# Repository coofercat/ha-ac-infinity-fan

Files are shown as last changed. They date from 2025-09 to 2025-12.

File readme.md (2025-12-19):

# HA AC Infinity Fan Controller

The AC Infinity Cloudline growing fans (such as the S4, S5, S6) are fantastic smart fans. They're made for growing rooms and the like, but also have a use in domestic bathrooms. They have temperature and humidistat probes and can be programmed to speed up the fan as humidity increases. This makes them ideal to suck out the steam after a shower.

Side note: in the UK, all houses have to have an Energy Performance Certificate (EPC). EPCs now take into account things like ventilation, energy efficiency etc. Smart fans can help improve your EPC because you can show continuous forced ventilation, and variable speed extraction of humidity (which is better than running on
a timer, or even at full speed to a fixed humidity level).

Whilst AC Infinity fans can connect to Wifi or Bluetooth, sadly, they do not (yet) come with any publicly accessible API. As such, the likes of Home Assistant can't directly interface with them. Hopefully one day AC Infinity will see the value in such things, but until then, we have to use different methods to hook these fans into our home automation.

## About This Project

__Note: The suggested PCB suffers from electrical noise problems. It worked fine on the desk, but in actual use, it's not really good enough. I'm working on a solution...__

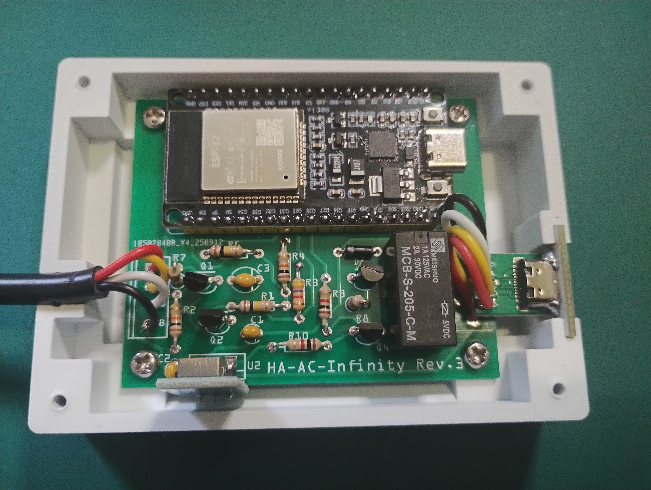
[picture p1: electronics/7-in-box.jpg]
[](electronics/7-in-box.jpg)

This project aims to provide Home Assistant integration to AC Infinity Cloudline fans, but also aims to leave all the original manufacturer functionality in place. This allows for flexibility and creativity in Home Assistant, but leaves the fans "as intended" and usable by any future owners.

In terms of implementation, this project puts some electronics "between" the AC Infinity controller display and the fan itself. It's entirely powered by the fan, and unless Home Assistant instructs it otherwise, it just passes AC Infinity signals from the controller to the fan completely unaltered.

Home Assistant is able to read the speed requested by the AC Infinity controller, the actual speed of the fan itself (via its tach signal), and is able to "switch out" the controller and provide signals to drive the fan itself if needed. There is no way to read the temperature or humidistat sensors on the AC Infinity controller though (if that's required, other projects may be more to your liking than this one).

Since this project was for use in bathrooms, we also provides an optional Boost Button. That is, a button which can be used to request 30 minutes of maximum speed fan extraction, perhaps to remove smells. The button is completely optional and does not require Home Assistant to be running or available to make it work.

The whole thing is based around an ESP32-32S WROOM (CP2012) and ESPHome. A few pins of the ESP are used as inputs and outputs, the bluetooth is used as a BLE receiver (for the Boost Button), the Wifi connects it to Home Assistant.

## Documentation

- [About the Electronics](electronics/readme.md)
  - [Electronics 3D Printed box](electronics/3d-printer/readme.md)
- [About the Boost Button](boost-button/readme.md)
  - [Boost Button 3d Printed box](boot-button/3d-printer/readme.md)
- [About the ESPHomeSoftware](esphome/readme.md)
- [FAQ](faq.md)
- [License](LICENSE.md)

## Authors Note

This project is Creative Commons licensed, so you're pretty much free to do what you like with it, so long as you credit the original author. If you do make it, we'd love to hear about what you're doing with it though, so please do get in contact.

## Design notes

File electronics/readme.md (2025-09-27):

# HA AC Infinity Electronics

The electronics for the HA AC Infinity project require a few components:

- An ESP32-32S WROOM board (eg. https://www.amazon.co.uk/dp/B0DQ51N5B1)
- A USB-C socket (eg. https://www.amazon.co.uk/dp/B0D59Y34ZF)
- A USB-C plug (eg. https://www.amazon.co.uk/dp/B09V273Z8Z)
- Some 4-core wire (eg. https://www.amazon.co.uk/dp/B0C14L4W14)
- Two 3D printed parts to make the box (although other boxes are also possible)
- Four M3 x 5mm and 4 M3 x 12mm screws to hold it together
- Some short lengths of general purpose multi-strand hookup wire (ideally in a few different colours)

There is also a whole [Bill Of Materials](https://html-preview.github.io/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) (BOM) for the electronic circuit. The circuit uses mostly generic, easy to source through-hole components. It's relatively easy to solder together. The transistors I used are 2N3904, and I used a buck module (https://www.amazon.co.uk/dp/B081JMJZG6) instead of a regular 7805 voltage regulator (if you do use a 7805, you will also need a heatsink). The relay is a generic 5V coil, DPDT (I had some of these already). The BOM lists JP1 and JP2, but these are not needed - they're just holes for attaching wires.

I also had PCBs made, which is optional but recommended (you get a lot of electrical noise in this circuit, so trying to make it work on a breadboard or stripboard is likely to be difficult). There is a [Fritzing file](ac-infinity-esphome.fzz) and [exported Gerber files](ha-ac-infinity-gerber-export/) available if you want to make a PCB.

## Making the Electronics

### USB Connectors

AC Infinity misuse USB connectors for their proprietary connections. Their system is absolutely not compatible with any genuine USB devices, and will likely catastrophically damage them if you are foolish enough to connect them to it.

For the project, we need a lead with a plug on the end of it and a socket. The plug likely can't fit any plastic covers on it, and the lead should be long enough to allow you to put the box of electronics somewhere near to the fan's controller. In my case they're all hidden away, so I've used a short cable. Longer cables are likely possible because the signals used aren't particularly complex.

| Socket & Plug | AC Infinity | Colour Coding |
| --- | --- | --- |
| V | +10V | Red |
| D+ | Tach Signal | Yellow |
| D- | PWM | White |
| G | Ground | Black |

Note the labelling on the plug and socket is really small - be careful where you're soldering!

For the plug, cut about 30cm of the four core cable. Remove about 15mm of sleeve from one end to expose the individual wires. Then strip all four wires to a couple of millimeters (I found it easier to strip to about 5mm and trim them after tinning). Tin the ends, and tin all four pads on the plug. Then you can connect the wires to the pads relatively easily. At the other end of the cable, remove maybe 15-20mm of sleeve and then strip the wires to about 5mm (don't tin them though).

For the socket, you need four 50mm lengths of multi-strand wire. Strip one end to a couple of millimeters, insert into the holes on the socket and solder into place. Again, strip the other end to maybe 5mm, but don't tin them.

| USB Plug Wiring | USB Socket Wiring |
| --- | --- |
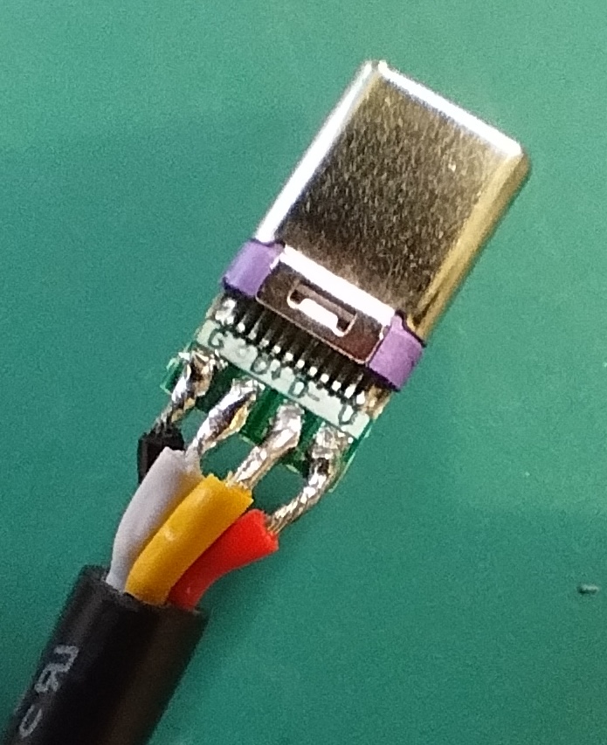
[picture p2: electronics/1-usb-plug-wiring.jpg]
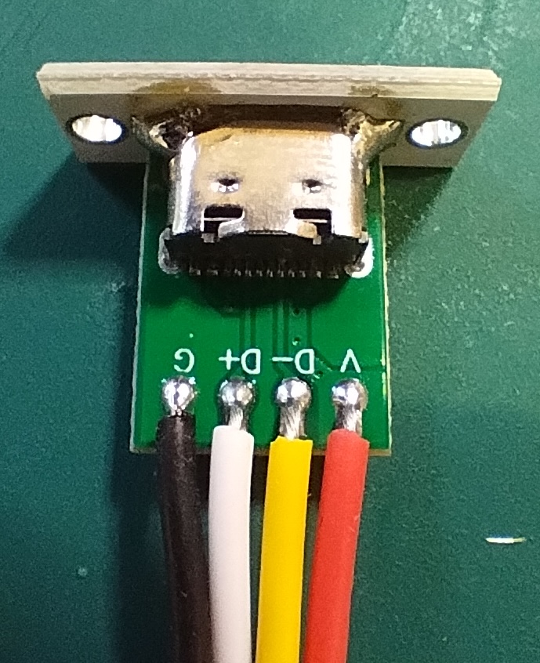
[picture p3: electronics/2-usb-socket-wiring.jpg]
| [](1-usb-plug-wiring.jpg) | [](2-usb-socket-wiring.jpg) |

### Making the PCB

The PCB uses through-hole components, which are hopefully easy to fit and solder. Most components lie against the board, although a few resistors are vertical (R7 & R8). Please note that if a 7805 voltage regulator is used (instead of a compatible module) then a heat sink will be required.

See the [Bill Of Materials](https://html-preview.github.io/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) for a full list of components required and where to fit them. Note that JP1 and JP2 are not required - instead their holes can be used to connect wires from the USB sockets (see below).

| Step | Step |
| --- | --- |
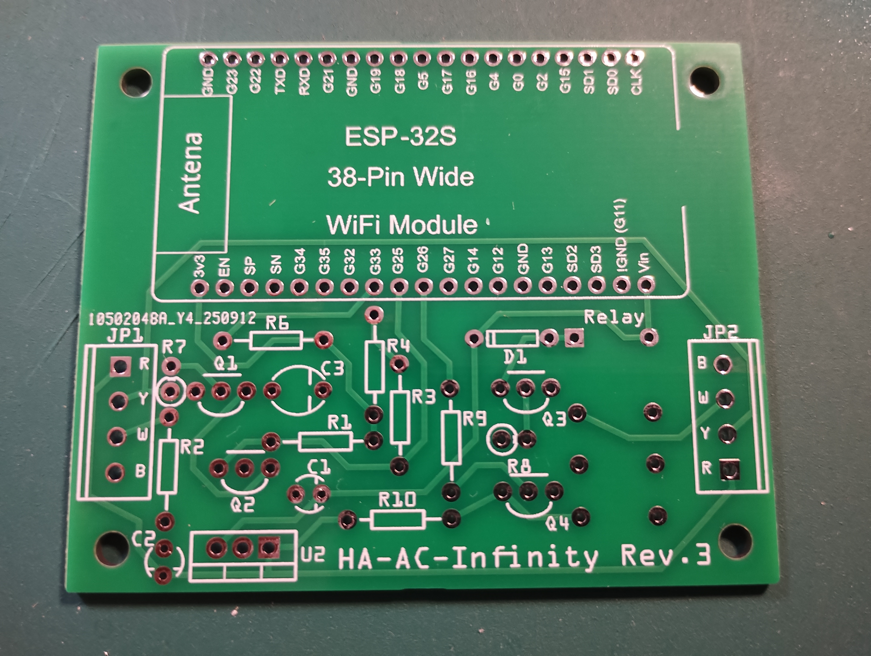
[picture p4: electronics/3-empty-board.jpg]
| [](3-empty-board.jpg) | Start with an empty board...  |
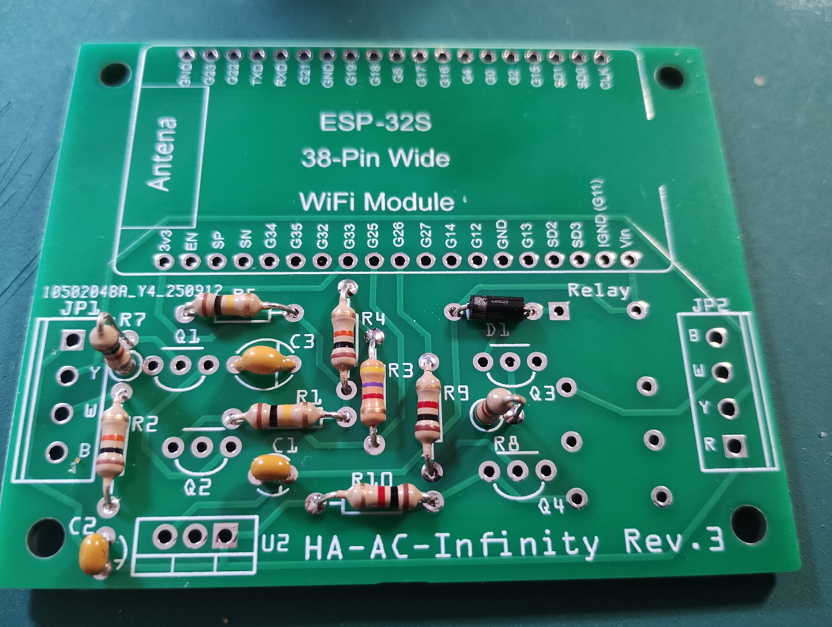
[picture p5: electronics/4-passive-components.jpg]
| [](4-passive-components.jpg) | Add the passive components... |
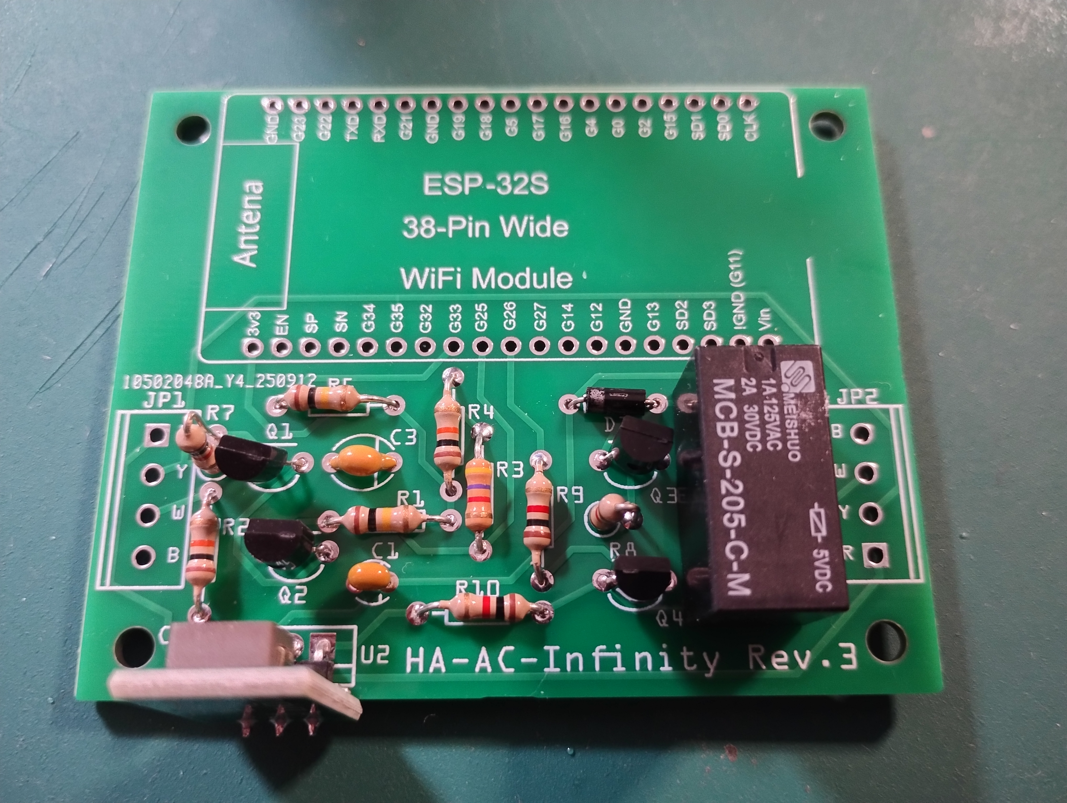
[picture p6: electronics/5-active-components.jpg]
| [](5-active-components.jpg) | Add the active components...  |

### Connecting the USB Connectors

The left hand JP1 connector is used to connect the USB plug, on the 4 core cable. The right hand, JP2 connector is used to connect the USB socket, on four short multi-strand wires. Note the colour coding of the holes on the PCB, from the top of the board to the bottom:

| JP1 | JP2 |
| --- | --- |
| Red | Black  |
| Yellow | White  |
| White  | Yellow |
| Black  | Red |

Once assesmbled it should look like this:

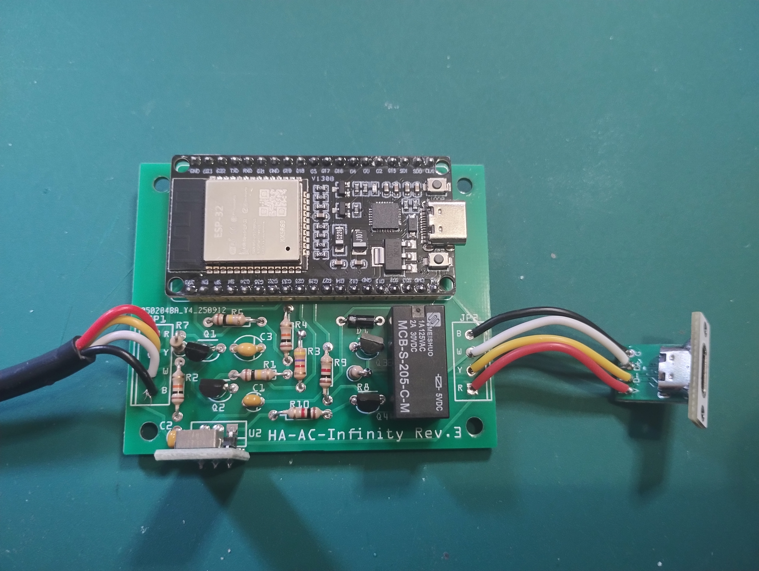
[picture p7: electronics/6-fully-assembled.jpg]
[](6-fully-assembled.jpg)

### Fitting the board into the box

The board should screw into the box using four M3 5mm self-tapping screws. The 4 core cable should fit into the cable gland, and be held into place by a strain-relief grip. The USB socket should fit into the slot on the side of the box.

[](7-in-box.jpg)

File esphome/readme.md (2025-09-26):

# ESPHome Software

This software requires [ESPHome](https://esphome.io/) to be on the ESP32 before it can be used.

Once ESPHome is installed, the [device.yaml](device.yaml) file can be pasted into the device configuration. Some secrets need to be added to ESPHome, or else edit the yaml appropriately.

The code has a configurable section:

```
  name: "ac-infinity-fan-1"
  friendly_name: "ac-infinity-fan-1"
  ap_ssid: "ha-ac-infinity-fan-1"
  ap_password: "ha-ac-infinity"
  ha_api_encryption_key: !secret ha_api_encryption
  esphome_ota_password: !secret esphome_ota_password
  wifi_connect_ssid: !secret wifi_ssid
  wifi_connect_password: !secret wifi_password
  boost_minutes: "30"
  boost_button_mac_address: "00:11:22:33:44:55"
  calibration_mode: "false"
```

| Variable | Comments |
| --- | --- |
| name | The ESPHome/HA name for the device |
| friendly_name | The longer name used to describe the device in the UI |
| ap_ssid | The network name (SSID) to create if wifi cannot be found during boot up |
| ap_password | The network password of the mini access point created if wifi not found during boot up |
| ha_api_encryption_key | The Home Assistant API encryption key _where to get this?_ |
| esphome_ota_password | The password used by ESPHome when making Over The Air (OTA) wireless connections |
| wifi_connect_ssid | The network name (SSID) of the wifi network to connect to on boot up |
| wifi_connect_password | The network password of the wifi used to connect to on boot up |
| boost_minutes | The number of minutes to run the fan during Boost Mode (specify as a string with quotes around the number) |
| boost_button_mac_address | A MAC address to listen for, if found, activate Boost Mode |
| calibration_mode | Boolean to enable calibration mode (see below) |

## Calibration

The project uses whole numbers from 0-10 to denote the speed of the fan (in the same way as AC Infinity do in their app and on the controller). To make these match with the AC Infinity scale, we have to calibrate the software to match.

Calibration Mode shows a decimal part of the integer speed number. This is a fraction of the "distance" between the lower and upper thresholds of a given speed number. For example, if the lower threshold was 1000 and the upper was 2000, and the current reading was 1230, then the decimal would be .23.

Working out thresholds requires some experimentation and measurements of the actual values received from the fan and controller. Hopefully the values provided here work in most cases, buf if you find selecting (say) speed 3 in the controller shows speed 4 in the Home Assistant UI, then some calibration may be required.

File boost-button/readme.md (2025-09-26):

# HA-AC-Infinity Boost Button

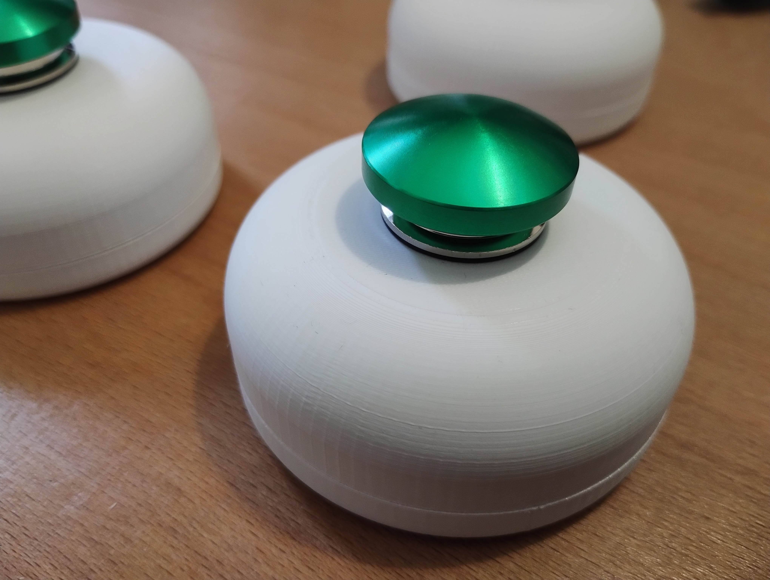
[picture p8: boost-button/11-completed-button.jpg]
[](11-completed-button.jpg)

The Boost Button is a way to request the fan comes on (at full speed)
for a period of time (currently programmed at 30 minutes). It's a
physical device with a big button on the top which can be put somewhere
in the bathroom, should anyone, er, "make smells" and want to have
some ventilation.

Internally, the button is made of some bought components:

- A so-called "iTag" key finder (BLE beacon), such as these: https://www.amazon.co.uk/dp/B0FH64TKKL
- A 22mm mushroom button, such as these: https://www.amazon.co.uk/dp/B0DB28T1KS
- Two AAA single battery holders, such as these: https://www.amazon.co.uk/dp/B0B9NJ14WL
- Some 3D printed parts to make a sort of "hockey puck" box
- Some small screws to hold things together (eg. 4 off M2.3 x 5-8mm round head, 2 off M2.3 x 5mm countersunk)

There are full [instructions](instructions.md) for how to construct the button.

## About the BLE Beacon

The "ITag" devices are super-cheap (you get four in pack for less than one of the "better" brands).
They're probably not very good at being key finders (mainly because the phone app they use is pretty poor),
but they work really well for this project.

These devices identify as "iTag", manufactured by "Ubiquitous Computing Technology Corporation". My scanner says they use the "Legacy" scanning type, and are LE only. They're connectable, and there are some capabilities once connected. The original phone app is able to make them beep remotely, so there's presumably a capability to do that in there somewhere.

The main feature that they need is that they must BLE beacon as soon as they're powered up. Some
brands do this, some do not (those tend to need you to press the button to start the beaconing
process). The Boostt Button has a single button, which we use to isolate power from the beacon to
specifically stop it beaconing (and to save battery). As such, we really do need it to start
beaconing as soon as we power it up. Some other brands of key finder can have their buttons
permanently pressed to do the same thing - if you can't find the iTag type, then some
experimentation may be needed.

You may want to look into using a phone app BLE scanner. I've been using nRF Connect (by Nordic Semiconductor). It seems to do a good job of finding these sorts of tags and giving out as much information as they have in them.

## About the Box

The box for this is 3D printed. You can of course use a different box, and if you use different
beacons, you're going to have to modify the box at the very least, if not design it differently.
The same is true if you use a different type of button.

In terms of printing, the box needs support to be able to print it. On my BambuLabs A1, with a single
filament, the support was sufficiently easy to remove and left good enough quality inside (all the
outside surfaces print beautifully). If you've got multiple materials and can do fancy support then
you're likely to get better internal quality than I did, but I'm not sure it's all that necessary.

The box is made of two parts which screw together from the bottom. You need to undo four small screws to be able to change the batteries.

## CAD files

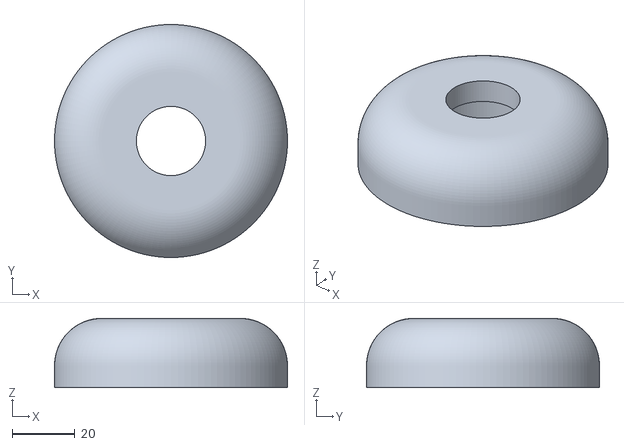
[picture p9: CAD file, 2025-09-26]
boost-button/3d-printer/button-top.stl
74.0 x 74.0 x 22.0

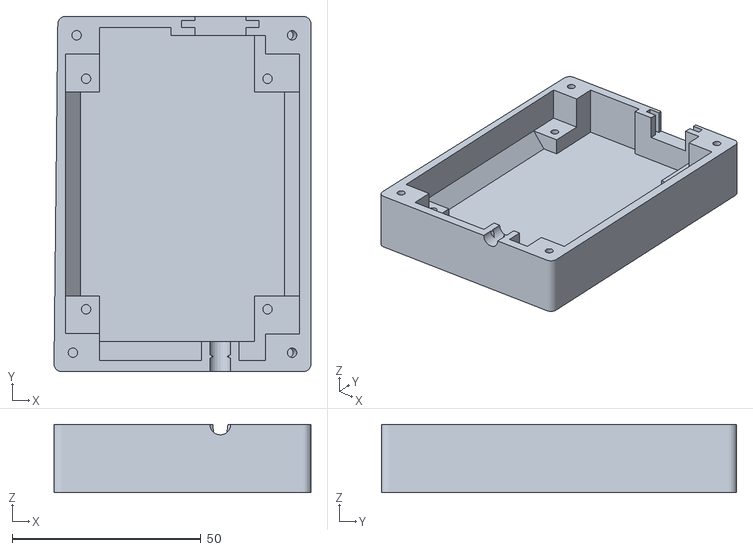
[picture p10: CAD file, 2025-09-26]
electronics/3d-printer/electronics-box-bottom.stl
68.0 x 94.0 x 18.0

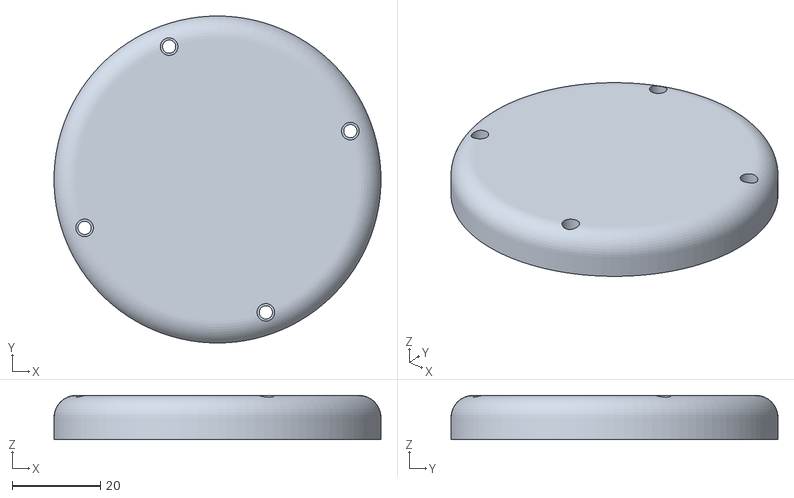
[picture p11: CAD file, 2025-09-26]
boost-button/3d-printer/button-bottom.stl
74.0 x 74.0 x 10.0

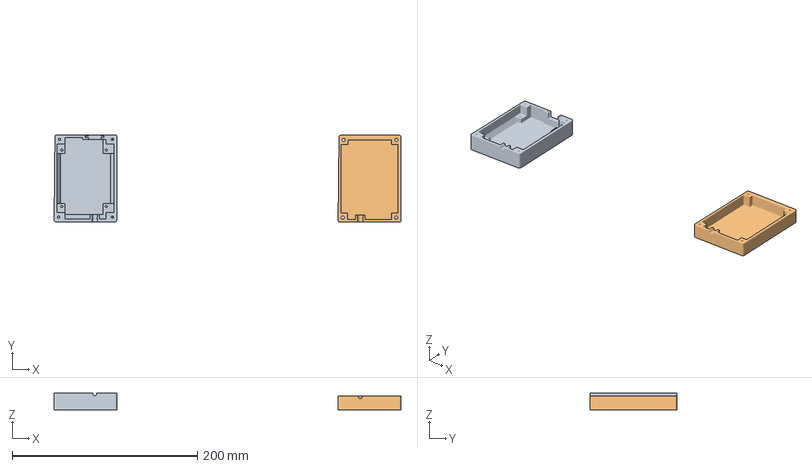
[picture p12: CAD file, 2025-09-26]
electronics/3d-printer/electronics-box.3mf
374.8 x 94.5 x 18.0 mm
electronics-box-bottom.stl
electronics-box-top.stl

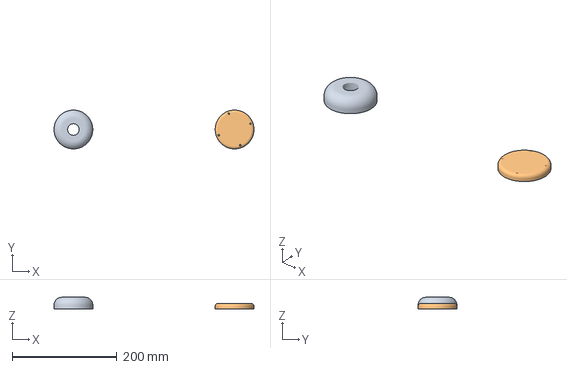
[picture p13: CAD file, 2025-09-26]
boost-button/3d-printer/boost-button.3mf
381.2 x 74.0 x 22.0 mm
button-top.stl
button-bottom.stl

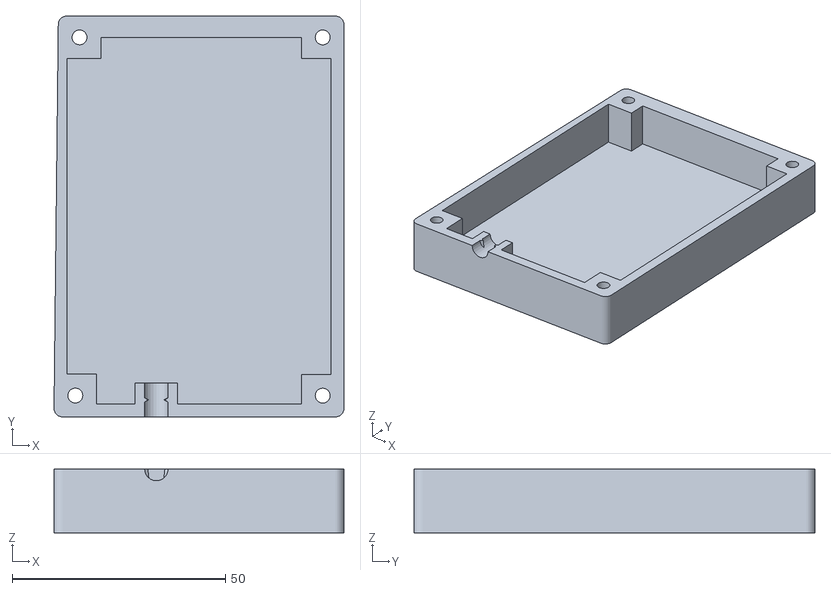
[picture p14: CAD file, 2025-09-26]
electronics/3d-printer/electronics-box-top.stl
68.0 x 94.0 x 15.0

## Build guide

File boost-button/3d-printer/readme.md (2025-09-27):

# Boost Button 3D Printed box

Three files are provided:

| File | Comments |
| --- | --- |
| [button-bottom.stl](button-bottom.stl) | The bottom lid of the button box, in STL format |
| [button-top.stl] (button-top.stl) | The top rounded part of the box, in STL format |
| [boost-button.3mf](boost-button.3mf) | Both top and bottom of the box in a Bambu Studio project file |

Both the top and bottom part need support to print successfully. On my Bambu AI with a single filament, support in "Normal Tree mode" worked well. Otherwise no special settings are required. Some experimentation may be required.

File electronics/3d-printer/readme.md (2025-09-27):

# Electronics 3D Printed Box

Three files are provided:

| File | Comments |
| --- | --- |
| [electronics-box-bottom.stl](electronics-box-bottom.stl) | The bottom of the box, in STL format |
| [electronics-box-top.stl](electronics-box-top.stl) | The top lid of the box, in STL format |
| [electronics-box.3mf](electronics-box.3mf) | Both top and bottom of the box in a Bambu Studio project file |

The electronics box is pretty easy to print in PLA filament (any colour). No special settings were required to print it successfully several times.

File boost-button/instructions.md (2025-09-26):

# Making the Boost Button

| Instructions | Picture |
| --- | --- |
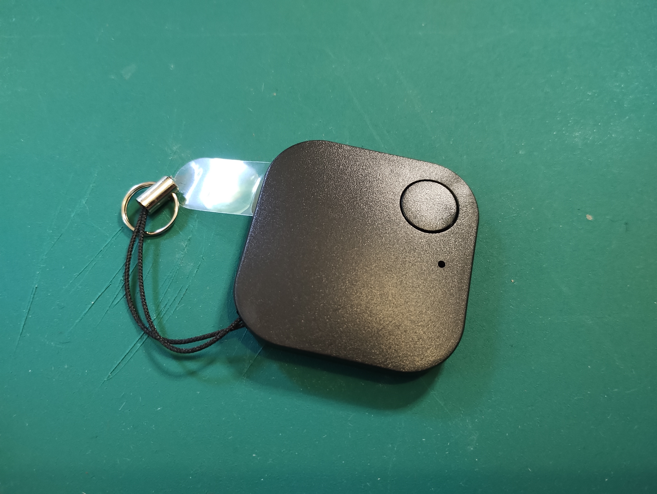
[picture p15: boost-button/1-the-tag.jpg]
| Firstly, take one of the keyfind fobs... | [](11-the-tag.jpg) |
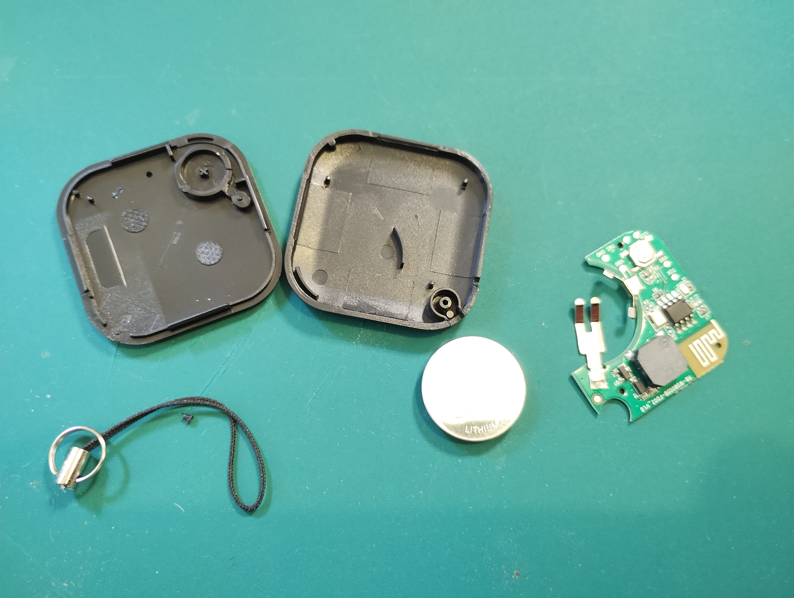
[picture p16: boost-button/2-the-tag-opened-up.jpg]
| ...and open it up. You can prize the two parts of the case apart, perhaps by inserting a small screwdriver in between them around the lanyard loop.| [](2-the-tag-opened-up.jpg) |
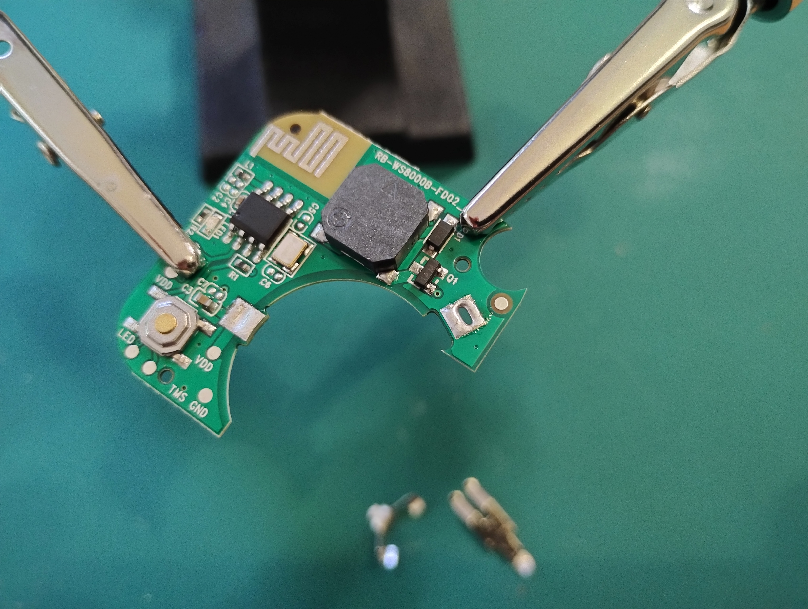
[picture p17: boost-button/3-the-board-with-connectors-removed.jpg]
| Take the circuit board and desolder the battery connectors. | [](3-the-board-with-connectors-removed.jpg) |
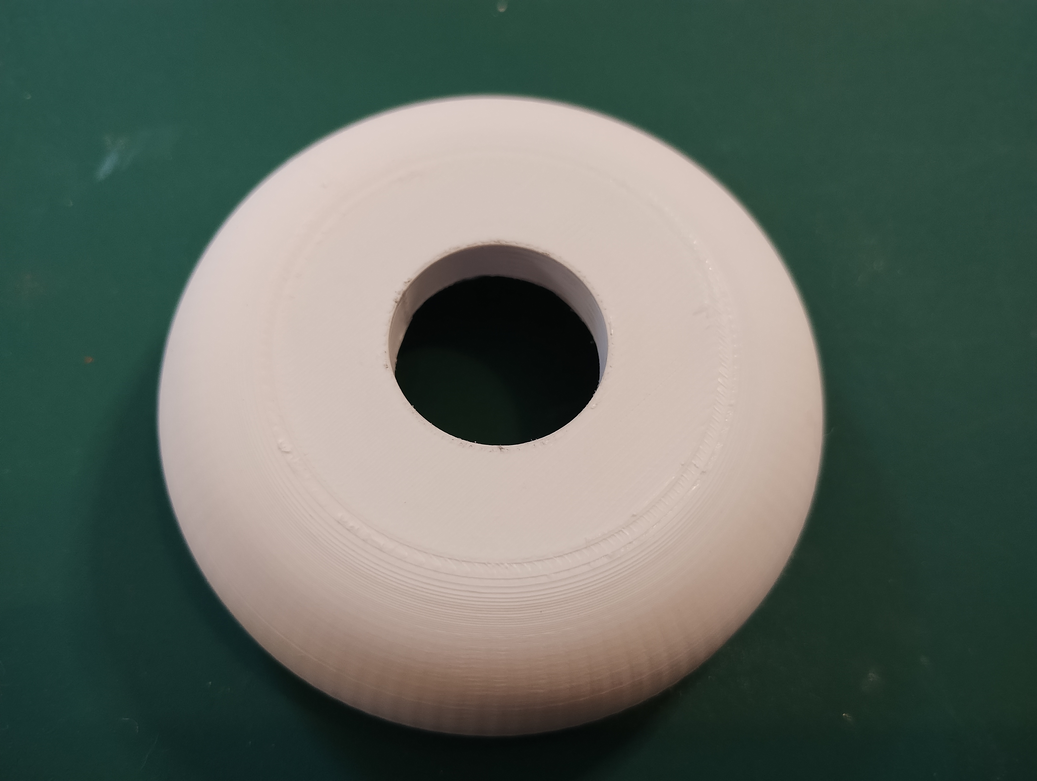
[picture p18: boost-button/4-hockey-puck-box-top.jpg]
| Take the top part of the hockey puck box... | [](4-hockey-puck-box-top.jpg) |
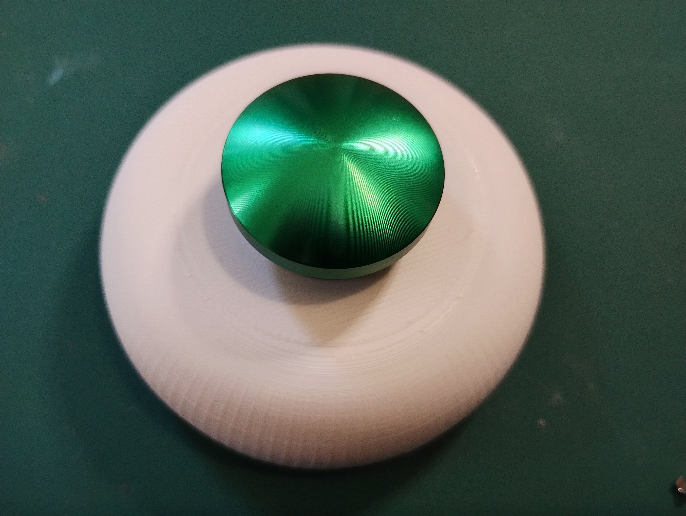
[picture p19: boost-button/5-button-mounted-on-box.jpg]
| Fit the mushroom button into the box. | [](5-button-mounted-on-box.jpg) |
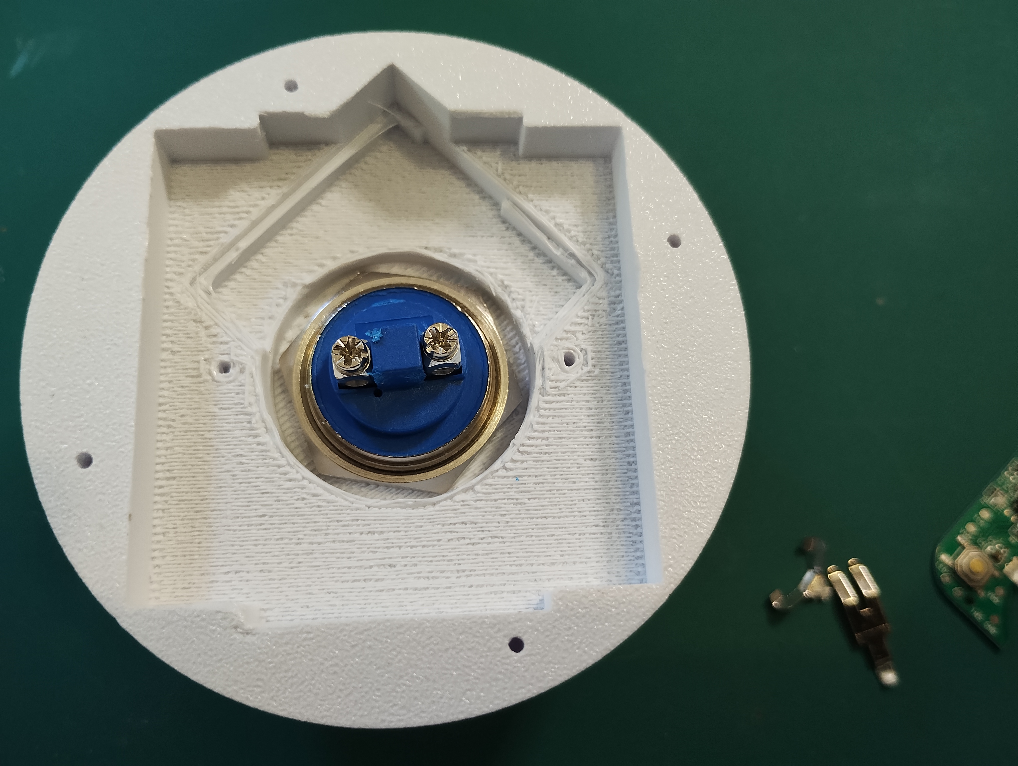
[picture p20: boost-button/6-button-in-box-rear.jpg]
| ...and tighten the retaining nut as far as possible. You may want to use a small screwdriver to rotate the nut, whilst pushing the button into the box to compress the rubber seals. | [](6-button-in-box-rear.jpg) |
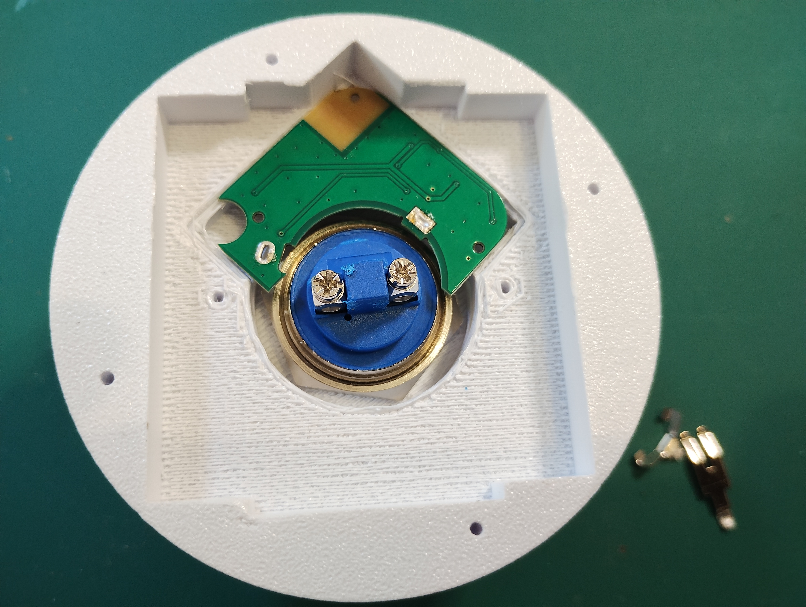
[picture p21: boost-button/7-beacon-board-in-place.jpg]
| Insert the beacon board in the inside of the case. | [](7-beacon-board-in-place.jpg) |
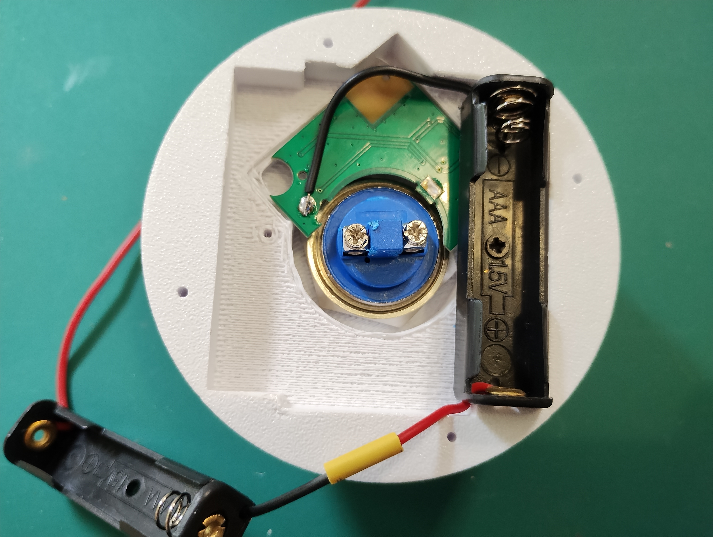
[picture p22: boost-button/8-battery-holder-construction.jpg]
| Next, insert one of the two battery holders and screw it into place. Cut the black (negative) wire and solder it to the beacon board. Cut and join the red wire and the black wire of the second battery holder together. | [](8-battery-holder-construction.jpg) |
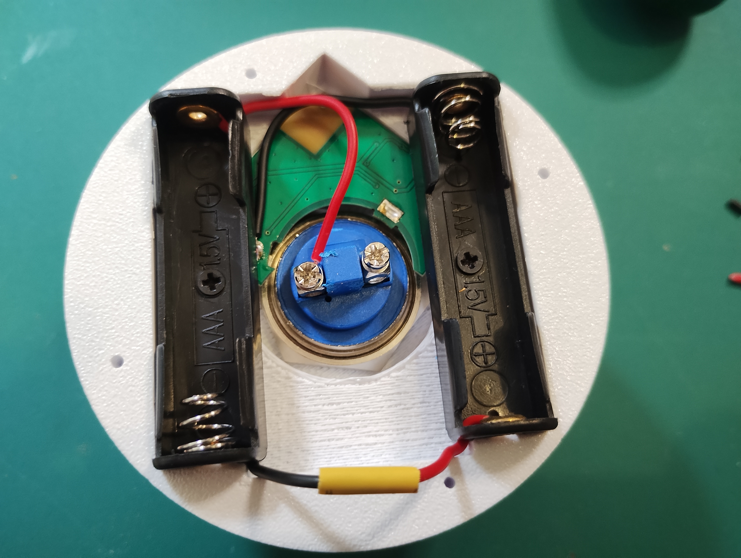
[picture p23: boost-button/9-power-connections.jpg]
| Mount the second battery holder and screw it into place. This will secure the beacon board into place. Cut the red wire and screw it into one of the switch terminals. | [](9-power-connections.jpg) |
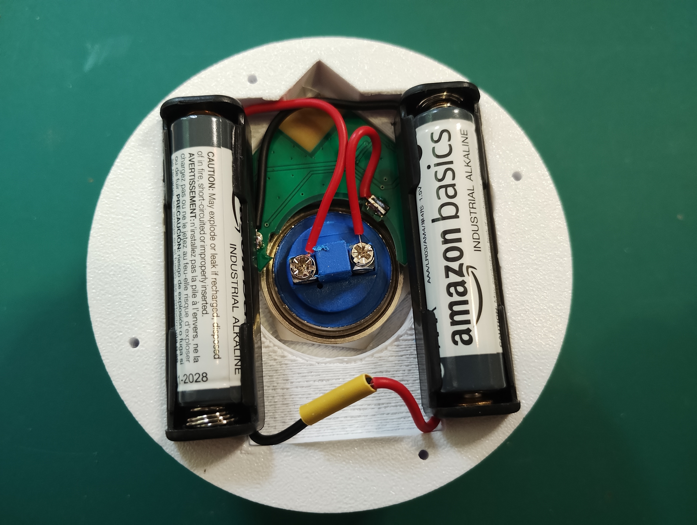
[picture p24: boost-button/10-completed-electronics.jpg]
| Solder some wire to the battery terminal on the beacon board and screw the other end into the second switch terminal. Finally, screw the bottom of the hockey puck to the top using four small screws. | [](10-completed-electronics.jpg) |
| The boost button is now complete. | [](10-completed-button.jpg) |

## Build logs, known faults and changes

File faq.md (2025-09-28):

# HA AC Infinity Frequently Asked Questions

## Why have a 'takeover' and 'pass through'? Why not control the fan directly?

The aim of this project was to be as "low impact" as possible, and to let the fans operate as the manufacturer intended _unless_ the user specifically wants something different. If the fans get built into a house, then
this avoids "the house that Jack built" problems, and lets any future owner use the fans as normal if they want to. It also lets the fans operate via the controller (and perhaps the AC Infinity phone app), even if home automation is unavailable.

## Why did you use a relay? Surely $some_other_solution is better?

Originally I tried to get the circuit to work with a a 74HC00, acting as a switch. I had problems with getting the PWM signals from the controller and from the ESP32 to work properly, so changed it to use a relay instead. There are quite probably better solid state solutions available, and I'd be happy to see any working improvements.

## What transistors are needed to make the electronics?

You can use any reasonably fast, low power transistors. I used 2N3904s, but any NPN transistors with a similar sort of capability will do fine.

## Can you/how do you read temperature and humidity from the controller?

This project does not have access to the temperature or humidity (or other readings) the controller has available. Unless AC Infinity make some sort of API, we have to work without.

Other projects completely replace the AC Infinity controller, and so the sensor probe plugs into them instead of the controller. Those projects do have access to the environmental readings, but then become the sole source of control of the fan (which isn't what this project aimed to do).

## What other projects are there?

Google may be a more definitive and up to date way to find this sort of thing, but here are a few to get started:

- https://github.com/dalinicus/homeassistant-acinfinity
- https://github.com/hunterjm/ac-infinity-hacs
- https://community.home-assistant.io/t/ac-infinity-controller-67-bluetooth-temp-humidity-fan-pwm
- https://github.com/ex-nerd/esphome-shelly-cloudline

## What can Home Assistant do to the fan with this project?

HA can read the controller's speed signal and it can read the fan's tach speed signal. Therefore it can determine what the controller has requested, and what the fan is actually doing. Further, it is able to disconnect the controller's speed request signal and insert its own instead, thus it can make the fan run at a different speed than the controller may be set to at the time.

## Can this work with other fans in the AC Infinity range?

I don't know for sure. The CloudLine range all work the same way, so are all compatible. Other lines may also work, but I haven't tested them. I'd welcome any proven information on any of them.

## Can this work with multiple fans connected to the same controller?

Yes, although each set of electronics only works with one fan. Therefore you'd need a set of electronics for each fan you want to control.

## Can I use this project with some other product or different manufacturer?

Probably not. The AC Infinity connections and signals are proprietary and very much not USB standard, so it's unlikely any other manufacturer would happen to have adopted the same specifications. Products other than fans are also unlikely to work with this without modification.

## Can you make parts of this project for me?

Sadly, no. You may be able to find companies that can 3D print things for you, someone like JLCPCB can make the PCB for you and may even assemble the circuit board for you though. At the end of the day, this is a "DIY" project, so you may have to solve some problems yourself.

## What is the Boost Button?

The Boost Button is a physical button which sends a signal to the HA AC Infinity electronics. On receipt, the electronics takes control of the fan, and requests it runs at full speed for 30 minutes. At the end of that time, it goes back to however it was before the button was pushed. None of this needs Home Assistant, so it works 'offline' if necessary. It can be triggered via Home Assistant as well, so if you have another way to "push the button", it's possible to do that too.

## I've heard you should use opto-isolators with AC Infinity fans because of concerns about mains...?

I've heard this too. I'm no expert, but my take on it is that if mains does appear on any of the four power/signal lines, it's going to cause a whole world of problems for the fan and controller, so whatever happens to this additional electronics is really the least of those problems. It would also call into question the general safety and quality of the fan product as a whole, probably making it unsuitable for any domestic use.

## Can I reprogramme the ESP32 while its soldered on the board?

Yes you can. For most updates you can use ESPHome's wireless Over The Air (OTA) feature. If you need to directly connect with a USB cable you can do this, but disconnect the board from the AC Infinity while you do so. You will need to remove the board from the box to get access to the ESP32's USB socket.

## My fan says it's running at some speed, but Home Assistant says it's a different speed

You may need to calibrate your electronics with the fan and controller you have. See [ESPHome/readme](esphome/readme.md) for more details.

## How is this project licensed? Do I need to pay for it or anything else?

The project is Creative Commons licensed, so you can pretty much do what you like with it, so long as you credit the original author. You don't need to pay to use it.

## Do I need to tell you if I've made any of this project?

No, but I'd love to hear from you if you do. It's be great to hear what you're using it for.

## What if my question isn't answered?

Feel free to get in touch (via Github's 'Issues').
